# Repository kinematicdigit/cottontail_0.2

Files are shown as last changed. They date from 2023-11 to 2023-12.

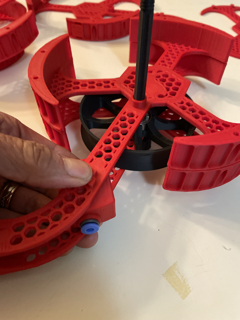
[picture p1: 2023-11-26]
IMG/IMG_6659 Small.png

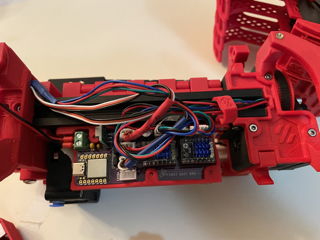
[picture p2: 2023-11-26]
IMG/IMG_6661 Small.png

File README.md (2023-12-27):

## BETA CYCLE IS COMPLETE - RELEASE IS NOW FOUND AT THE OFFICIAL ERCF V2 PAGE: https://github.com/Enraged-Rabbit-Community/ERCF_v2 



Cotton Tail buffer system will attach directly to the Sturdy Bunny upgraded ERCF and is designed to work with any number of filament blocks you choose (the initial test phase will go up to 9). 

The primary goal of this project was to reduce as much resistance in the path and to remove any inconsistencies in calibration. It works with Triple Decky but will work with whatever top hat/filament block design you want. In fact, there is no limitation to the design, and it also may remove the need for magnets in them altogether. There is a spring in the couplers to alleviate all pressure on the magnets.

This system is also designed to reduce the buffer length, which will help reduce friction on the entire system. There will also be optional QoL features to work with the new BTT MMB Can board.
Features:
- Large central buffer wheel - reduces the filament's natural shape - each wheel comes pre-notched to make loading filament easier.
- Inline connection - connects to the 2020 extrusion arm
- Short Buffer Length - Can operate as low as 500mm in buffer Length
- Reduced resistance - Tests up to 200 mm/s (with Galileo 2 extruder) - may do less or more depending on your extruder motor
- Improved encoder accuracy - makes all resistance more consistent for better encoder performance and less torque needed
- Stackable Arm - Each arm is stackable for whatever combination of gates you want. They are optimized for strength and weight and provide access for loading and unloading filament
- Uses most parts from ERCP -  if you already have a kit, most parts should be interchangeable.
- Filament Detector - Each coupler has a filament detector built in. This is optional and will interface with the new BTT MMB Can board. 
- Filament indicator - Future QoL option that will include the ability to light up each gate to tell you if it is loaded/active and empty/out of filament.

###

***

### BOM (Each arm group/channel):

* (8) 8mm M3 screws
* (1) 16mm M3 screw
* (1) 25mm M3 screw
* (1) M3 threaded inserts (M3x5x4mm) Heat Sets
* PTFE Tubing (4mm OD/3MM ID recommended)
* (1) 608 ZZ Bearing (same as ERCP - skateboard bearings will work as well)
* (1) ECAS
* (2) M3 Hammerhead T-Nuts (for attaching to 2020 extrusions)

### End cap (with integrated MMB CASE) needs:

* (6) 8mm M3 screws
* (5) 25mm M3 screw (1) for non MMB
* (4) M3 threaded inserts (M3x5x4mm) Heat Sets (0) for non MMB

**The optional MMB version build requires:**

(1) BTT MMB Can board
(1) Microswitch per arm
(1) 5.5 mm ball bearing per arm
(2) 12mm M2 BHCS screws per arm
(1) Button Neopixels per arm

***

## Building the ERCT

### **Instructions**

**PRINT SETTINGS**

.25mm first layer, .2mm Layer Height
4 Perimeters (top, bottom, walls

Arms should be printed at .2 layer height, with 4 walls and 10% lightning infill. This will significantly reduce the amount of filament used. ABS is the recommended material or PETG.

Wheels should be printed on a smooth plate, or if you use a textured plate you may need to run it on some sandpaper afterwards to avoid too much contact with the arm. There will always be a small chance of some rubbing, but with careful pressure on the hubs when installing, you shouldn't have any major resistance.

The rest of the parts can be printed with 20-30% gyroid infill.

|   | Start with your printed channel arm and add a 4 mm-deep M3 heatset installed into the back of the arm. Be careful not to go too far past the dovetail channel- it's better to be shy than to go over. |
| ---: | --- |
|   | Print the correct length axial screw. The files are labelled for how many channels. They are longer than needed in case you need to put a bypass divider or extra support. Use the matching nut and work it through the acme screw to make it smooth. A brass brush can also be used to clean it up a little. It is recommended if you make more than 9 channels, to self-source a trapezoidal bar screw (also known as ACME screw). T8, Pitch 2 is a common one. You can also use a traditional screw. Make sure to get matching nuts to add to each end for those builds. |
|   | Load the axial through the first arm. |
|  | The 608 bearings should slide in with just a tiny bit of resistance. |
|   | Make sure the filament loading holes are as pictured, and load the axial from the flat side of the wheel. |
|   | When pushing down on the axial, put your thumbs on each side of the bearing and push down with moderate force. Don't push too hard. If it doesn't go on, use a little sandpaper on the axial to reduce it. It is a tight fit but should slide on. Your pressure on the bearings will ensure the wheel is as balanced as possible. There's a very tiny bit of gap between the wheel and the side of the arm. Don't worry too much if it isn't perfect, but you can try to balance it and spin it to check. |
|  | Preload the M3 Hammerhead T-Nuts onto the mounting bracket. Don't screw in too tight as you need to turn the nuts easily to load into the v-slots of the 2020 extrusion. |
|  | Load the mount onto the arm. The dovetail is snug but should slide on with some pressure. Once seated add the M3 16mm screw to secure it. |
|  | Squeeze the printed spring (the spring goes towards the ECAS side) and slide into the slot on the sloped side.&#xA; |
|  | Add ECAS fitting in the hole. It should snap-in and firm press.&#xA; |
|  | line up the coupler as pictured to the three receiving pins. It should press fit with a small bit of resistance. Repeat the next channel arm until all is loaded. |
|  | When you reach the final channel, you will add the end cap and install the final M3 25mm screw. |
|  | Secure all 6 screws, which enter at an angle. They self-tap into the plastic, so don't over-tighten or you'll strip the plastic. These install and reinstall multiple times if you don't over-tighten.  &#xA; |
|  | The next step is prepping the ERCF. If you have wiring clips, remove them and free all your wires. |
|  | Line up the t-nuts as best you can. Make sure you didn't wind them all the way down. The screws should have enough friction to hold them in place to make this part easier for you. It should sit right on the shoulder and slip in. If not, jiggle the arms a little; it should all mate perfectly. Grab your driver and turn, and it should tighten right away. If not, back off a quick half-turn and turn the back the other way to load the nut in place. |
|   | The last set of steps starts by cutting around 85mm of tube which should leave around 10mm of tube sticking out of the coupler block. |
|  | Insert the cut PTFE tube from the rear of the assembly. Push lightly in the spring, and it should feed through. |
|  | Line up to the channel and press into the ECAS on the filament block. |
|  | The rest of the tube can be trimmed to around 10mm. |
|  | The wires can now be routed against the mounting brackets and you can use zip ties to secure it. |

***

**LOADING THE BUFFER**

|  | To load the buffer, filament from your reverse Bowden. Try your best to work with the natural curl of the filament and feed it till you see it pop out on top. |
| ---: | :--- |
|  | Grab it from up top, and curl it back into one of the multiple filament loading holes located along one side of the buffer wheel. |
|  | Turn the wheel until you have the number of rows needed for your tube length between the ERCF encoder and the tool head (to calculate the right length, measure the tube and divide by 230mm. This will equal the number of rows you need to wrap around the wheel - maximum of 7). |
|  | Back below, grab the filament on the wheel and pull it out. |
|  | Give yourself some length (about 30 cm). |
|  | Feed back into the tube located there. |
|  | It will feed through, and you should feel some resistance from the trap; press on the top hat to help it through. |
|  | The final step is to push the filament flush to the opening so it doesn’t catch on the selector. That’s it. Load it all up, and away you go! |

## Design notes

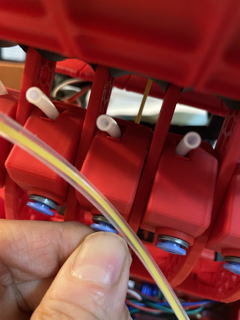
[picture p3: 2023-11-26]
IMG/IMG_6672 Small.png

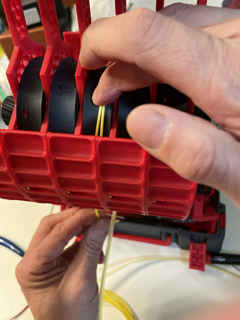
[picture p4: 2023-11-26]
IMG/IMG_6676 Small.png

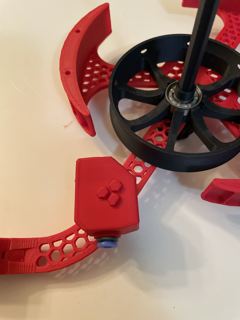
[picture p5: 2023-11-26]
IMG/IMG_6658 Small.png

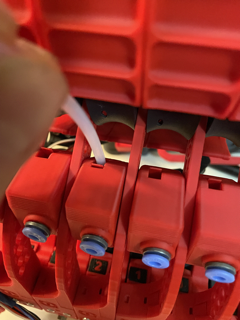
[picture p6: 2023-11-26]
IMG/IMG_6666 Small.png

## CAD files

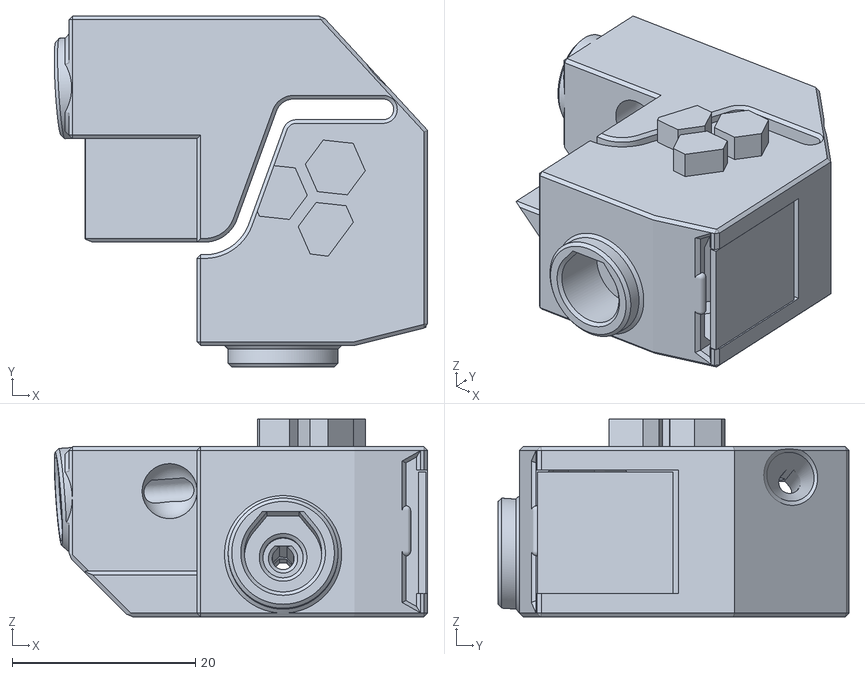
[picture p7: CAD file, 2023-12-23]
stls/Hybrid_coupler_block.stl
40.8 x 38.3 x 21.6

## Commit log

2023-11-26 Beta 0.2 Update
    Major restructuring of folders, and now new build options including Thumper Block support.
    [5mm arm bushing.stl, 5mm arm end cap bushing.stl, 625 case end cap.stl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]
2023-11-26 Beta 0.2 Updates
    [[a]support_arm_endcap_MMB_case_top.stl]
2023-11-26 Updated Cottontail to latests repos and organization.
    [[a]BTT_MMB support_arm_endcap_case_top.stl, [a]axial_spacer.stl, [a]axial_spacer_bypass.stl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]
2023-11-26 Coupler Block updated to Roll-in nuts
    final update. Coupler Block has been updated to Roll-in Nuts instead of T-Nuts. Moved the T-nut version to depreciated folder if people want to use that still.
    [[a]coupler_block.stl, [a]knut_T8_p2_tolerance+1.0.stl, [a]support_arm_mount_t-nut.stl]
2023-11-26 Final Updates
    [[a]axial_spacer.stl, [a]axial_spacer_bypass.stl, [a]coupler_block.stl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]
2023-11-26 Final Update
    [[a]coupler_block.stl]
2023-11-26 Added 12 Gate Axle
    [axle_12_double_thread.stl]
2023-11-27 Temporary closure of options
    [LED_Soldering_tool_holder_by_jose.stl, [a]BTT_MMB_Bottom_Bracket.stl, [a]BTT_MMB_Bottom_Bracket_universal.stl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]
2023-11-27 Reorganized folders and 180 degree option/TB options
    [LED_Soldering_tool_holder_by_jose.stl, [a]BTT_MMB_Bottom_Bracket.stl, [a]BTT_MMB_Bottom_Bracket_universal.stl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]
2023-11-27 minor updates
    [Max volumetric speed test.stl, [a]BTT_MMB support_arm_endcap_case_top.stl, [a]BTT_MMB_Bottom_Bracket.stl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]
2023-11-28 4-8 Double threaded Axle
    [[a]kaxle_5.stl, [a]kaxle_6.stl, [a]kaxle_7.stl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]
2023-11-28 Renamed files to follow Voron naming conventions
    [5mm arm bushing.stl, 5mm arm end cap bushing.stl, 625 case end cap.stl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]
2023-11-28 Renamed to follow Voron Naming Conventions.
    [[a]coupler_block.stl, [black]LED_carrier.stl, [t]coupler_block_MMB.stl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]
2023-11-28 Renamed to follow Voron Naming Conventions
    [5mm arm bushing.stl, 5mm arm end cap bushing.stl, 625 case end cap.stl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]
2023-11-30 Print Orientation correction for Coupler MMB
    [[t]_Coupler_Block_MMB_xN.stl]
2023-12-01 Minor Corrections
    [[a]_Arm_Anchor_PTFE_Foot.stl, [a]_Arm_Anchor_PTFE_x2.step, [a]_Arm_Anchor_PTFE_x2.stl]
2023-12-01 re added depreciated box
    [[a]BTT_MMB_Bottom_Bracket.stl, [a]BTT_MMB_Top_Lid_180.stl, [a]BTT_MMB_Top_Lid_Standard.stl]
2023-12-03 updated double plate version to correct height
2023-12-21 BETA FILES REMOVED FOR OFFICIAL LAUNCH
    [5mm arm bushing.stl, 5mm arm end cap bushing.stl, 625 case end cap.stl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]
2023-12-23 For beta testers only, makes beta compatible with new ERCF V2
    Merry Christmas to all Beta Team Testers.
    This is the only part that needs to be update to make your current version work with the recently released ERCF V2 work (I haven't tested it so print one to be sure it fits). It should line up just fine, and the switches are in the correct position for it to work with the latest version of Happy Hare.
    The older version with switches are not compatible with the latest version of Happy Hare, so if you do have that version, either disable the switches or print this new version.
    Thanks again to all beta testers and happy holidays!
    [Hybrid_coupler_block.stl]
